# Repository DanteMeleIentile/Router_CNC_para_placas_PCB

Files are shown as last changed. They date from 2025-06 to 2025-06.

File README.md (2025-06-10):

# Router CNC para placas PCBs
Proyecto desarrollado por el Grupo 1 en la materia **Prácticas Profesionalizantes** del **Instituto Industrial Luis A. Huergo**.

**Año:** 2020

[Acceder a la carpeta del proyecto en Google Drive](https://drive.google.com/drive/folders/1eBrdESxct46WMWiOsJgtsmofHZRLYTOU?usp=sharing)

## Docentes
- Osvaldo Ivani
- Sebastían Amago Prato
- Martín A. Ricciardelli
- Juan Martín Hermida

## Estudiantes (Grupo 1)
- Dante G. Mele Ientile (Project Manager)
- León A. Martin
- Hernán A. Silva
- Nicolás L. Fertonani
- Laureano M. Rivera Pascua

---
> _"Lo que comenzó siendo una simple idea de una “Solución Electromecánica”, se
convirtió en un ensamble 3D con más de 1000 componentes, en 100 planos tanto mecánicos
como eléctricos y electrónicos, en más de 60 diagramas de operaciones, en 4 circuitos de
control, generando más de 50 GB de datos y un sinfín de avances y resultados completamente
realizadores._
>
>  _Todo esto fue el resultado de más de **5000 horas de trabajo**, en un período de prácticamente
8 meses, preservando día a día la Constancia, la Exigencia y el Compromiso."_
---

<p align="center">
  Logo Huergo
</p>

## Licencia
Este proyecto (incluyendo código, planos, documentación técnica y modelos 3D) está disponible bajo la licencia [MIT](./LICENSE).

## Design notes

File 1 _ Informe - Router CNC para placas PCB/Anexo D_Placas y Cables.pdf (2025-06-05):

## Cables y Terminales

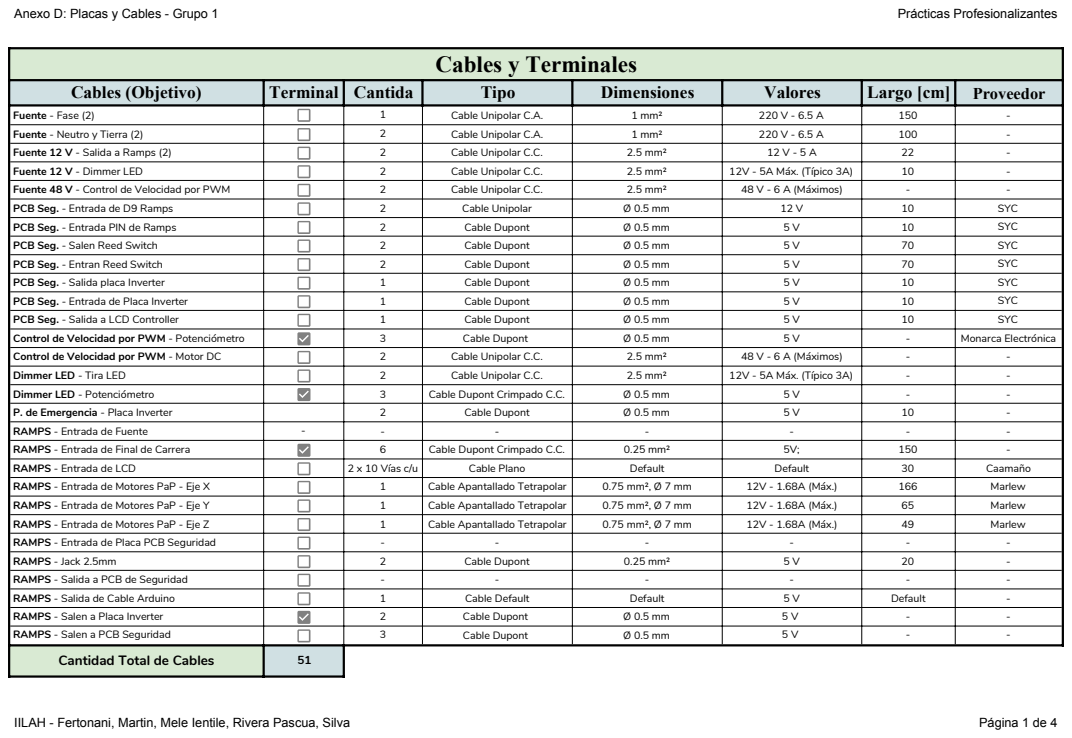
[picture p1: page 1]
Anexo D: Placas y Cables - Grupo 1; Prácticas Profesionalizantes; IILAH - Fertonani, Martin, Mele Ientile, Rivera Pascua, Silva; Página 1 de 4

Cables (Objetivo) | Terminal | Cantida | Tipo | Dimensiones | Valores | Largo [cm] | Proveedor

Fuente - Fase (2) | | 1 | Cable Unipolar C.A. | 1 mm² | 220 V - 6.5 A | 150 | -
Fuente - Neutro y Tierra (2) | | 2 | Cable Unipolar C.A. | 1 mm² | 220 V - 6.5 A | 100 | -
Fuente 12 V - Salida a Ramps (2) | | 2 | Cable Unipolar C.C. | 2.5 mm² | 12 V - 5 A | 22 | -
Fuente 12 V - Dimmer LED | | 2 | Cable Unipolar C.C. | 2.5 mm² | 12V - 5A Máx. (Típico 3A) | 10 | -
Fuente 48 V - Control de Velocidad por PWM | | 2 | Cable Unipolar C.C. | 2.5 mm² | 48 V - 6 A (Máximos) | - | -
PCB Seg. - Entrada de D9 Ramps | | 2 | Cable Unipolar | Ø 0.5 mm | 12 V | 10 | SYC
PCB Seg. - Entrada PIN de Ramps | | 2 | Cable Dupont | Ø 0.5 mm | 5 V | 10 | SYC
PCB Seg. - Salen Reed Switch | | 2 | Cable Dupont | Ø 0.5 mm | 5 V | 70 | SYC
PCB Seg. - Entran Reed Switch | | 2 | Cable Dupont | Ø 0.5 mm | 5 V | 70 | SYC
PCB Seg. - Salida placa Inverter | | 1 | Cable Dupont | Ø 0.5 mm | 5 V | 10 | SYC
PCB Seg. - Entrada de Placa Inverter | | 1 | Cable Dupont | Ø 0.5 mm | 5 V | 10 | SYC
PCB Seg. - Salida a LCD Controller | | 1 | Cable Dupont | Ø 0.5 mm | 5 V | 10 | SYC
Control de Velocidad por PWM - Potenciómetro | | 3 | Cable Dupont | Ø 0.5 mm | 5 V | - | Monarca Electrónica
Control de Velocidad por PWM - Motor DC | | 2 | Cable Unipolar C.C. | 2.5 mm² | 48 V - 6 A (Máximos) | - | -
Dimmer LED - Tira LED | | 2 | Cable Unipolar C.C. | 2.5 mm² | 12V - 5A Máx. (Típico 3A) | - | -
Dimmer LED - Potenciómetro | | 3 | Cable Dupont Crimpado C.C. | Ø 0.5 mm | 5 V | - | -
P. de Emergencia - Placa Inverter | | 2 | Cable Dupont | Ø 0.5 mm | 5 V | 10 | -
RAMPS - Entrada de Fuente | - | - | - | - | - | - | -
RAMPS - Entrada de Final de Carrera | | 6 | Cable Dupont Crimpado C.C. | 0.25 mm² | 5V; | 150 | -
RAMPS - Entrada de LCD | | 2 x 10 Vías c/u | Cable Plano | Default | Default | 30 | Caamaño
RAMPS - Entrada de Motores PaP - Eje X | | 1 | Cable Apantallado Tetrapolar | 0.75 mm², Ø 7 mm | 12V - 1.68A (Máx.) | 166 | Marlew
RAMPS - Entrada de Motores PaP - Eje Y | | 1 | Cable Apantallado Tetrapolar | 0.75 mm², Ø 7 mm | 12V - 1.68A (Máx.) | 65 | Marlew
RAMPS - Entrada de Motores PaP - Eje Z | | 1 | Cable Apantallado Tetrapolar | 0.75 mm², Ø 7 mm | 12V - 1.68A (Máx.) | 49 | Marlew
RAMPS - Entrada de Placa PCB Seguridad | | - | - | - | - | - | -
RAMPS - Jack 2.5mm | | 2 | Cable Dupont | 0.25 mm² | 5 V | 20 | -
RAMPS - Salida a PCB de Seguridad | | - | - | - | - | - | -
RAMPS - Salida de Cable Arduino | | 1 | Cable Default | Default | 5 V | Default | -
RAMPS - Salen a Placa Inverter | | 2 | Cable Dupont | Ø 0.5 mm | 5 V | - | -
RAMPS - Salen a PCB Seguridad | | 3 | Cable Dupont | Ø 0.5 mm | 5 V | - | -
Cantidad Total de Cables | 51

IILAH - Fertonani, Martin, Mele Ientile, Rivera Pascua, Silva | Página 2 de 4

## Componentes Placa Dimmer para Tira LED

Componente | Cant. | Caracteristicas | Ø broca | Código SYC | Link Datasheet
Resistencia | 1 | 1 kΩ, 1/4W | 1 | CR25S-1K | http://www.sycelectronica.com.ar/pasivos/CR25S-XX.pdf
Resistencia Gate MosFET | 1 | 56 Ω, 1/4 W | 1 | CR25S-56 | http://www.sycelectronica.com.ar/pasivos/CR25S-XX.pdf
Capacitor | 2 | 10 nF, 50V, disco cerámico | 1 | CD103-50
Capacitor | 1 | 1 µF, Radial, electrolítico aluminio | 1 | R1M50 | http://www.sycelectronica.com.ar/pasivos/RXXXMXX.pdf
Diodo rápido | 2 | 1N4148, de señal, Vr = 100 V | 1 | 1N4148 | http://www.sycelectronica.com.ar/semiconductores/1N4148.pdf
Potenciómetro Lineal | 1 | 1 MΩ | 1 | POTE-105-LIN | N.e.
LM555 | 1 | Ver datasheet | 1 | EK500A-2P | http://www.sycelectronica.com.ar/semiconductores/LM555.pdf
MOSFET | 1 | IRFZ48N, Rdson = 14 mΩ, Vds = 55 V | 1,5 | IRFZ48N | http://www.sycelectronica.com.ar/semiconductores/IRFZ48N.pdf
Bornera | 2 | 2 polos, paso = 5 mm | 1 | EK500A-2P | http://www.sycelectronica.com.ar/borneras/EK500A-XXP.pdf
Conector para Potenciómetro | 1 | Macho, 3 vías | 2 | 2317SJ-03 | http://www.sycelectronica.com.ar/conectores/PWXX.pdf
Conector para Potenciómetro | 1 | Hembra, 3 vías | 1 | PHUXX | http://www.sycelectronica.com.ar/conectores/PHUXX.pdf
Disipador | 1 | 15 x 15 x 15 | - | D-9075D | http://www.sycelectronica.com.ar/accesorios/DISIPADORES.pdf
Terminal | 3 | En rollo | - | PHUT | http://www.sycelectronica.com.ar/conectores/PHUT.pdf
Agujeros de Sujección | 4 | - | 3,5 | - | -

IILAH - Fertonani, Martin, Mele Ientile, Rivera Pascua, Silva | Página 3 de 4

## Componentes Placa Seguridad

Componente | Cant. | Caracteristicas | Ø broca | Código - SYC | Link Datasheet
Compuerta NAND | 1 | Quad NAND | 1 | 74LS00 | http://www.sycelectronica.com.ar/semiconductores/74LS00.pdf
Compuerta AND | 1 | Quad AND | 1 | 74LS08 | http://www.sycelectronica.com.ar/semiconductores/74LS08.pdf
Capacitor | 1 | 47 µF, 5x11, 16V, Electrolítico de aluminio | 1 | R47M16 | http://www.sycelectronica.com.ar/pasivos/RXXXMXX.pdf
Diodo Zener | 1 | 1N4733 | 1 | ZEN-1W-5V1 | http://www.sycelectronica.com.ar/semiconductores/ZEN-1W-XXV.pdf
Jumper con Extractor | 1 | Con extrractor | 1 | MJ02-L | http://www.sycelectronica.com.ar/conectores/MJ02-X.pdf
Pin Header | 1 | Tira de 16 | 1 | SCP16-SF | http://www.sycelectronica.com.ar/conectores/SCP16-SF.pdf
Diodo LED | 1 | Rojo, 5 mm | 1 | LED-010-15010 | http://www.sycelectronica.com.ar/optoelectronica/LED-010-15010.pdf
Resistencia Pull Down | 6 | 1 KΩ | 1 | CR25S-5K6 | http://www.sycelectronica.com.ar/pasivos/CR25S-XX.pdf
Resistencia Capacitor | 1 | 270 Ω | 1 | CR25S-270 | http://www.sycelectronica.com.ar/pasivos/CR25S-XX.pdf
Resistencia LED | 1 | 220 Ω | 1 | CR25S-220 | http://www.sycelectronica.com.ar/pasivos/CR25S-XX.pdf
Resistencia Zener | 1 | 1 KΩ | 1 | CR25S-1K | http://www.sycelectronica.com.ar/pasivos/CR25S-XX.pdf
Bornera para Cables Motor DC | 1 | 2 polos, paso = 5 mm | 2 | EK500A-2P | http://www.sycelectronica.com.ar/borneras/EK500A-XXP.pdf
Diodo Schottky | 1 | If: 1A, Vr: 30V | 1 | 1N5817 | http://www.sycelectronica.com.ar/semiconductores/1N5817-9.pdf
Relay | 1 | 12 V, 10 A | 1,5 | NT73-12 | http://www.sycelectronica.com.ar/electromecanicos/NT73-XX.pdf
Agujeros de Sujección | 4 | - | 3,5 | - | -

IILAH - Fertonani, Martin, Mele Ientile, Rivera Pascua, Silva | Página 4 de 4

## Componentes Placa Inverter

Componente | Cant. | Caracteristicas | Ø broca | Código - SYC | Link Datasheet
Compuerta NOT | 1 | Quad NAND | 1 | 74LS04 | http://www.sycelectronica.com.ar/semiconductores/74LS00.pdf
Resistencia Pull Down | 6 | 1 KΩ | 1 | CR25S-5K6 | http://www.sycelectronica.com.ar/pasivos/CR25S-XX.pdf
Pin Header | 1 | Tira de 16 | 2 | SCP16-SF | http://www.sycelectronica.com.ar/conectores/SCP16-SF.pdf
Agujeros de Fijación | 4 | Tira de 16 | 3,5 | SCP16-SF | http://www.sycelectronica.com.ar/conectores/SCP16-SF.pdf

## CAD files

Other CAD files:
8 _ Diseño 3D - Grupo 1 (Inventor)/Acolpe L para Soporte LED.ipt
8 _ Diseño 3D - Grupo 1 (Inventor)/Acople de Motor PAP.ipt
8 _ Diseño 3D - Grupo 1 (Inventor)/Acople de soporte de motor.ipt
8 _ Diseño 3D - Grupo 1 (Inventor)/Ala 1 Bisagra tipo Libro Chica.ipt
8 _ Diseño 3D - Grupo 1 (Inventor)/Ala 1 Bisagra tipo Libro Grande.ipt
8 _ Diseño 3D - Grupo 1 (Inventor)/Ala 1 Bisagra tipo T.ipt
8 _ Diseño 3D - Grupo 1 (Inventor)/Ala 2 Bisagra tipo Libro Chica.ipt
8 _ Diseño 3D - Grupo 1 (Inventor)/Ala 2 Bisagra tipo Libro Grande.ipt
8 _ Diseño 3D - Grupo 1 (Inventor)/Ala 2 Bisagra tipo T.ipt
8 _ Diseño 3D - Grupo 1 (Inventor)/Arandela Grower M4.ipt
8 _ Diseño 3D - Grupo 1 (Inventor)/Arandela Grower M8.ipt
8 _ Diseño 3D - Grupo 1 (Inventor)/Arandela Grower m6.ipt
8 _ Diseño 3D - Grupo 1 (Inventor)/Arandela Plana Tipo A DIN 125 - M4.ipt
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

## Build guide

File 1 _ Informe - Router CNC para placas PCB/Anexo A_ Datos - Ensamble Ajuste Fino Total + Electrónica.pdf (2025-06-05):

Anexo A: Datos - Ensamble Ajuste Fino Total + Electrónica - Grupo 1 | Prácticas Profesionalizantes
IILAH - Fertonani, Martin, Mele Ientile, Rivera Pascua, Silva | Página 1 de 12

# Subconjunto Inferior - Ensamble Ajuste Fino Total + Electrónica

Nombre de la Pieza | Cant. | Medias Finales | Material | Material Inventor | Código
Acople Rigído 5x8 - Eje Y | 1 | Ver hoja "Varios" | - | Flaked Satin - Blue | -
Buje para Guía | 4 | Ver hoja "Varios" | Resina Acetal | Acetal Resin White | G1-AC-01-A
Bandeja | 1 | 2 x 408 x 454 | Chapa de Al - Espesor 2mm | Al 1100 - H14 | G1 - A - 16
Buje para Tornillo - Eje Y | 1 | Ver hoja "Varios" | Latón | Brass, Soft Yellow | G1-ABC-01-A
Chaponete | 2 | 8 x 12 x 50 | Acero SAE 1020 | Steel, High Strenght, Low Alloy | G1 - A - 13
Culata | 1 | 10 x 50 x 390 | Aluminio | Aluminio 6061 | G1 - A - 02
Esquina de Bandeja | 4 | 2 x 14 x 60 | Chapa de Al - Espesor 2mm | Al 1100 - H14 | G1 - A - 17
Frente | 1 | 10 x 50 x 390 | Aluminio | Aluminio 6061 | G1 - A - 01
Guía de Bandeja Derecha | 1 | 2 x 52,7 x 425 | Chapa de Al - Espesor 2mm | Al 1100 - H14 | G1 - A - 15
Guía de Bandeja Izquierda | 1 | 3 x 52,7 x 425 | Chapa de Al - Espesor 2mm | Al 1100 - H14 | G1 - A - 14
Guía de Mesa | 2 | Ø:12,7; L:434 | Acero SAE 1040 Cromado | Steel, High Strenght, Low Alloy | G1 - A - 06
Lateral Der. | 1 | 10 x 50 x 434 | Aluminio | Aluminio 6061 | G1 - A - 04
Lateral Izq. | 1 | 10 x 50 x 434 | Aluminio | Aluminio 6061 | G1 - A - 03
Manija para Bandeja | 1 | Ver Catálogo | - | - | -
Mesa | 1 | 10 x 200 x 200 | Acero SAE 1020 | Steel Mid | G1 - A - 12
Motor Paso a Paso - Eje Y | 1 | Ver Catálogo | - | - | -
Pared Espaciador - Sub. Inferior | 2 | 10 x 16 x 42 | Aluminio | Aluminio 6061 | G1 - A - 08
Patas Regulables | 4 | Ver Catálogo - Tornillo M6 | Ver Catálogo | - | -
Resorte para Tuerca de Mesa | 1 | Ø:20; Largo: 20; Paso: 6; ØEspira: 3 | - | - | -
Soporte de Buje para Guía | 4 | 28 x 40 x 35 | Aluminio | Aluminio 6061 | G1 - A - 10
Soporte de Patas Regulables | 4 | 10 x 35 x 42 | Aluminio | Aluminio 6061 | G1 - A - 05
Soporte de Tuerca de Mesa | 1 | 40 x 50 x 42 | Aluminio | Aluminio 6061 | G1 - A - 11
Tapa para Buje | 8 | Ver "Varios" | Acero SAE 1040 Cromado | Steel, High Strenght, Low Alloy | G1-AC-02-A
Techo Espaciador - Sub. Inferior | 1 | 10 x 42 x 62 | Aluminio | Aluminio 6061 | G1 - A - 09
Tornillo de Mesa | 1 | D:12; L:434 | Acero SAE 1040 | Steel | G1 - A - 07
Tuerca de Mesa | 1 | Ver "Varios" | Latón | Brass, Soft Yellow | G1-AC-03-A

# Sujeciones

Nombre de la pieza | Cant. | Objetivo
Arandela Grower M6 | 4 | Guía con Frente/Culata
Arandela Plana M4 | 2 | Chaponete con Tornillo para Chaponete
Arandela Plana M6 | 4 | Guía con Frente/Culata
Remache POP D4 | 8 | Esquinas de Bandeja con Bandeja
Tornillo Allen C/Botón M3 L:8 | 16 | Tapa para Buje
Tornillo Allen C/Botón M4 L:10 | 6 | Guía de Bandeja con Lateral
Tornillo Allen C/Botón M6 L:20 | 8 | Frente /Culata con Laterales
Tornillo Allen C/Botón M6 L:20 | 4 | Guia Con Frente /Culata
Tornillo Allen C/Cilindrica M4 L:16 | 4 | Techo Espaciador con Motor PaP
Tornillo Allen C/Cilindrica M4 L:16 | 4 | Sop. de Tuerca con Mesa
Tornillo Allen C/Cilindrica M4 L:20 (opcional) | 2 | Chaponete con Mesa
Tornillo Allen C/Cilindrica M4 L:35 | 16 | Sop. de Buje con Mesa
Tornillo Allen C/Cilindrica M4 L:35 | 4 | Espaciador con Culata
Tornillo Allen C/Fresada M3 L:20 | 2 | Apoyo de Chaponete
Tornillo Allen C/Fresada M4 L:16 | 8 | Sop de Pata con Lateral
Tornillo Allen Gusano M3 L:16 | 2 | Tuerca con Sop. Tuerca
Tuerca Hexagonal M4 | 1 | Manija de Bandeja con Bandeja

Anexo A Datos - Ensamble Ajuste Fino Total + Electrónica - Grupo 1 | Prácticas Profesionalizantes
IILAH - Fertonani, Martin, Mele Ientile, Rivera Pascua, Silva | Página 2 de 12

# Subconjunto Puente - Ensamble Ajuste Fino Total + Electrónica

Pieza | Cant. | Medidas Finales | Material | Material Inventor | Código
Acople Rígido 5x8 - Eje X | 1 | Ver Catálogo | - | Flaked Satin - Blue | -
Buje para Tornillo - Eje X | 1 | Ver hoja "Varios" | Latón | Brass, Soft Yellow | G1-ABC-01-B
Columna Der. | 1 | 12 x 64,5 x 259,5 | Aluminio | Aluminio 6061 | G1 - B - 02
Columna Izq. | 1 | 12 x 64,5 x 259,5 | Aluminio | Aluminio 6061 | G1 - B - 01
Final de Carrera - Eje X | 1 | Ver Catálogo | - | - | -
Guías de Vínculo Cabezal | 2 | Ø:12,7; L:434 | Acero SAE 1040 Cromado | Steel, High Strenght, Low Alloy | G1 - B - 03
Motor Paso a Paso - Eje X | 1 | Ver Catálogo | - | - | -
Soporte de Final de Carrera - Eje X | 1 | 2 x 25,5 x 15 | Chapa de Al - Espesor 2mm | Al 1100 - H14 | G1 - B - 06
Tornillo de Vínculo Cabezal | 1 | Ø:12; L:338 | Acero SAE 1040 | Steel | G1 - B - 04
Travesaño Estructural | 1 | 10 x 50 x 410 | Aluminio | Aluminio 6061 | G1 - B - 05

# Sujeciones

Nombre de la pieza | Cant. | Objetivo
Arandela Grower M6 | 4 | Guía con Columna
Arandela Grower M6 | 4 | Travesaño con Columna
Arandela Grower M6 | 8 | Columna con Laterales
Arandela Plana M6 | 4 | Guía con Columna
Tornillo Allen C/Botón M3 L:8 | 2 | Sop. de Final de Carrera con Columna
Tornillo Allen C/Botón M4 L:20 | 4 | Soporte para Culata Carcasa a Travesaño
Tornillo Allen C/Botón M4 L:20 | 4 | Columna con Motor PaP
Tornillo Allen C/Botón M6 L:20 | 4 | Travesaño con Columna
Tornillo Allen C/Botón M6 L:20 | 4 | Guías con Columna
Tornillo Allen C/Botón M6 L:20 | 8 | Columna con Laterales
Tornillo Allen C/Cilindrica M2 L:12 | 2 | Sop. de Final de Carrera con F. de Carrera
Tuerca Hexagonal M2 | 2 | Sop. de Final de Carrera con F. de Carrera

IILAH - Fertonani, Martin, Mele Ientile, Rivera Pascua, Silva | Página 3 de 12

# Subconjunto Cabezal - Ensamble Ajuste Fino Total + Electrónica

Nombre de la pieza | Cant. | Medidas Finales | Material | Material Inventor | Código
Acople de Soporte de Motor | 1 | 42 x 70 x 70 | Aluminio | Aluminio 6061 | G1 - C - 12
Acople Rígido 5x8 - Eje Z | 1 | Ver hoja "Varios" | - | Flaked Satin - Blue | -
Bloque de Vínculo Cabezal | 1 | 25 x 70 x 150 | Aluminio | Aluminio 6061 | G1 - C - 1
Broca Punta de Lanza (opcional) | 1 | Ver Catálogo | - | - | -
Buje de Soporte de Motor | 4 | Ø:25; L:14 | Resina Acetal | Acetal Resin White | G1 - C - 13
Buje para Guía | 4 | Ver hoja "Varios" | Resina Acetal | Aluminium Polished | G1-AC-01-C
Buje para Tornillo - Eje Z | 1 | Ver hoja "Varios" | Latón | Brass, Soft Yellow | G1-ABC-01-C
Final de Carrera - Eje Z | 1 | Ver Catálogo | Chapa Al. - Esp.: 2mm | - | -
Guía de Soporte de Motor | 2 | Ø:12,7; L: 150 | Acero SAE 1040 Cromado | Steel, High Strenght, Low Alloy | G1 - C - 05
Motor Paso a Paso - Eje Z | 1 | Ver Catálogo | - | - | -
Pared Espacidor Izq. - Sub. Cabezal | 1 | 10 x 28 x 42 | Aluminio | Aluminio 6061 | G1 - C - 08
Pared Espacidor Der. - Sub. Cabezal | 1 | 10 x 28 x 42 | Aluminio | Aluminio 6061 | G1 - C - 09
Piso de Vínculo Cabezal | 1 | 10 x 70 x 55 | Aluminio | Aluminio 6061 | G1 - C - 04
Resorte para Tuerca de Vínculo Cabezal | 1 | Ø:20; Largo: 20; Paso: 6; ØEspira: 3 | - | - | -
Separador de Bujes | 2 | Ø:18,5; L:14 | Acero SAE 1040 Cromado | Steel, High Strenght, Low Alloy | G1 - C - 02
Motor DC | 1 | Ver Catálogo | - | Al. 6061 / Chrome Polished | -
Soporte de Motor | 1 | Ver Catálogo | - | Aluminio 6061 | -
Tapa para Buje | 4 | Ver hoja "Varios" | Acero SAE 1040 Cromado | Steel, High Strenght, Low Alloy | G1-AC-02-C
Techo de Vínculo Cabezal | 1 | 10 x 70 x 55 | Aluminio | Aluminio 6061 | G1 - C - 07
Techo Espaciador - Sub. Cabezal | 1 | 10 x 50 x 60 | Aluminio | Aluminio 6061 | G1 - C -10
Tornillo de Soporte de Motor | 1 | MF12x1,5; L:164 | Acero SAE 1040 | Steel | G1 - C - 06
Tuerca de Vínculo Cabezal | 1 | Ø:34; L:15 | Latón | Brass, Soft Yellow | G1-AC-03-C
Guía para Cable de Motor | 1 | 2 x 30 x 30 | Chapa Al. - Esp.: 2mm | Aluminio 1100 H14 | G1 - C - 11
Vertical de Vínculo Cabezal | 1 | 12 x 136 x 70 | Aluminio | Aluminio 6061 | G1 - C - 03

# Sujeciones

Nombre de la pieza | Cant. | Objetivo
Arandela Grower M6 | 4 | Guía con Techo y Piso de Vínculo Cabezal
Arandela Grower M8 | 4 | Acople de Soporte de Motor con Sop. de Motor
Arandela Plana M6 | 4 | Guía con Techo y Piso de Vínculo Cabezal
Tornillo Allen C/Botón M3 L:8 | 4 | Buje de Sop. de M. con Acople de Motor Dc
Tornillo Allen C/Botón M3 L:8 | 8 | Tapa de Buje con Bloque de Vínculo
Tornillo Allen C/Botón M3 L:8 | 2 | Guía para Cable de Motor con Pared Espacidor
Tornillo Allen C/Botón M6 L:16 | 8 | Vertical con Techo y Piso de Vínculo Cabezal
Tornillo Allen C/Botón M6 L:20 | 4 | Guía con Techo y Piso de Vínculo Cabezal
Tornillo Allen C/Botón M6 L:20 | 8 | Vertical con Bloque de Vínculo Cabezal
Tornillo Allen C/Botón M8 L:20 | 4 | Acople de Soporte de Motor con Sop. de Motor
Tornillo Allen C/Cilindrica M2 L:12 | 2 | Techo de Vínculo Cabezal con Final de Carrera
Tornillo Allen C/Cilíndrica M4 L:20 | 4 | Motor PaP con Techo de Espaciador
Tornillo Allen C/Cilindrica M4 L:45 | 4 | Paredes de Espaciador con Techo de Vínculo
Tornillo Allen Gusano M3 L:16 | 2 | Tuerca con Sop. Tuerca
Tornillo Allen Gusano M6 L:8 | 1 | Motor DC con Soporte de Motor

# Subconjunto Carcasa - Ensamble Ajuste Fino Total + Electrónica

Nombre de la pieza | Cant. | Medidas Finales | Material | Material Inventor | Código

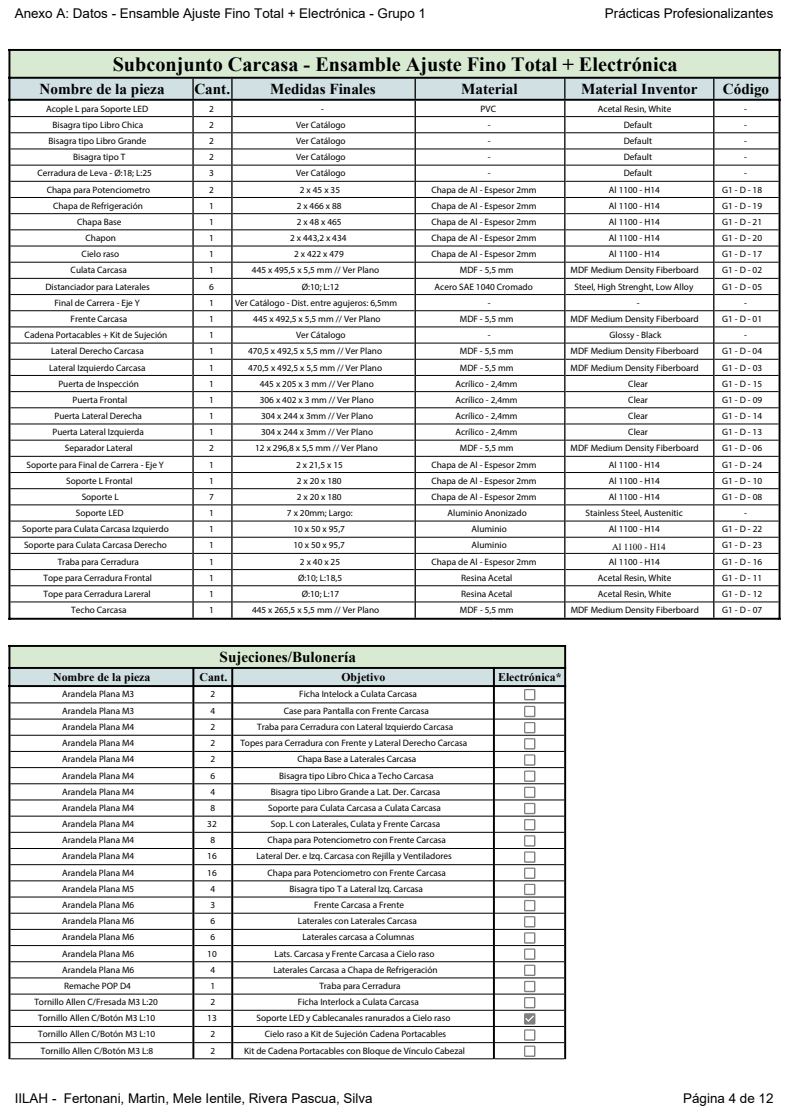
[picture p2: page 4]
IILAH - Fertonani, Martin, Mele Ientile, Rivera Pascua, Silva; Página 4 de 12

Acople L para Soporte LED | 2 | - | PVC | Acetal Resin, White | -
Bisagra tipo Libro Chica | 2 | Ver Catálogo | - | Default | -
Bisagra tipo Libro Grande | 2 | Ver Catálogo | - | Default | -
Bisagra tipo T | 2 | Ver Catálogo | - | Default | -

Cerradura de Leva - Ø:18; L:25 | 3 | Ver Catálogo | - | Default | -
Chapa para Potenciometro | 2 | 2 x 45 x 35 | Chapa de Al - Espesor 2mm | Al 1100 - H14 | G1 - D - 18
Chapa de Refrigeración | 1 | 2 x 466 x 88 | Chapa de Al - Espesor 2mm | Al 1100 - H14 | G1 - D - 19
Chapa Base | 1 | 2 x 48 x 465 | Chapa de Al - Espesor 2mm | Al 1100 - H14 | G1 - D - 21
Chapon | 1 | 2 x 443,2 x 434 | Chapa de Al - Espesor 2mm | Al 1100 - H14 | G1 - D - 20
Cielo raso | 1 | 2 x 422 x 479 | Chapa de Al - Espesor 2mm | Al 1100 - H14 | G1 - D - 17
Culata Carcasa | 1 | 445 x 495,5 x 5,5 mm // Ver Plano | MDF - 5,5 mm | MDF Medium Density Fiberboard | G1 - D - 02
Distanciador para Laterales | 6 | Ø:10; L:12 | Acero SAE 1040 Cromado | Steel, High Strenght, Low Alloy | G1 - D - 05
Final de Carrera - Eje Y | 1 | Ver Catálogo - Dist. entre agujeros: 6,5mm | - | - | -
Frente Carcasa | 1 | 445 x 492,5 x 5,5 mm // Ver Plano | MDF - 5,5 mm | MDF Medium Density Fiberboard | G1 - D - 01

Cadena Portacables + Kit de Sujeción | 1 | Ver Cátalogo | - | Glossy - Black | -
Lateral Derecho Carcasa | 1 | 470,5 x 492,5 x 5,5 mm // Ver Plano | MDF - 5,5 mm | MDF Medium Density Fiberboard | G1 - D - 04
Lateral Izquierdo Carcasa | 1 | 470,5 x 492,5 x 5,5 mm // Ver Plano | MDF - 5,5 mm | MDF Medium Density Fiberboard | G1 - D - 03
Puerta de Inspección | 1 | 445 x 205 x 3 mm // Ver Plano | Acrílico - 2,4mm | Clear | G1 - D - 15
Puerta Frontal | 1 | 306 x 402 x 3 mm // Ver Plano | Acrílico - 2,4mm | Clear | G1 - D - 09
Puerta Lateral Derecha | 1 | 304 x 244 x 3mm // Ver Plano | Acrílico - 2,4mm | Clear | G1 - D - 14
Puerta Lateral Izquierda | 1 | 304 x 244 x 3mm // Ver Plano | Acrílico - 2,4mm | Clear | G1 - D - 13
Separador Lateral | 2 | 12 x 296,8 x 5,5 mm // Ver Plano | MDF - 5,5 mm | MDF Medium Density Fiberboard | G1 - D - 06

Soporte para Final de Carrera - Eje Y | 1 | 2 x 21,5 x 15 | Chapa de Al - Espesor 2mm | Al 1100 - H14 | G1 - D - 24

Soporte L Frontal | 1 | 2 x 20 x 180 | Chapa de Al - Espesor 2mm | Al 1100 - H14 | G1 - D - 10
Soporte L | 7 | 2 x 20 x 180 | Chapa de Al - Espesor 2mm | Al 1100 - H14 | G1 - D - 08
Soporte LED | 1 | 7 x 20mm; Largo: | Aluminio Anonizado | Stainless Steel, Austenitic | -

Soporte para Culata Carcasa Izquierdo | 1 | 10 x 50 x 95,7 | Aluminio | Al 1100 - H14 | G1 - D - 22
Soporte para Culata Carcasa Derecho | 1 | 10 x 50 x 95,7 | Aluminio | Al 1100 - H14 | G1 - D - 23

Traba para Cerradura | 1 | 2 x 40 x 25 | Chapa de Al - Espesor 2mm | Al 1100 - H14 | G1 - D - 16
Tope para Cerradura Frontal | 1 | Ø:10; L:18,5 | Resina Acetal | Acetal Resin, White | G1 - D - 11
Tope para Cerradura Lareral | 1 | Ø:10; L:17 | Resina Acetal | Acetal Resin, White | G1 - D - 12
Techo Carcasa | 1 | 445 x 265,5 x 5,5 mm // Ver Plano | MDF - 5,5 mm | MDF Medium Density Fiberboard | G1 - D - 07

Sujeciones/Bulonería

Nombre de la pieza | Cant. | Objetivo | Electrónica*
Arandela Plana M3 | 2 | Ficha Intelock a Culata Carcasa
Arandela Plana M3 | 4 | Case para Pantalla con Frente Carcasa
Arandela Plana M4 | 2 | Traba para Cerradura con Lateral Izquierdo Carcasa
Arandela Plana M4 | 2 | Topes para Cerradura con Frente y Lateral Derecho Carcasa
Arandela Plana M4 | 2 | Chapa Base a Laterales Carcasa
Arandela Plana M4 | 6 | Bisagra tipo Libro Chica a Techo Carcasa
Arandela Plana M4 | 4 | Bisagra tipo Libro Grande a Lat. Der. Carcasa
Arandela Plana M4 | 8 | Soporte para Culata Carcasa a Culata Carcasa
Arandela Plana M4 | 32 | Sop. L con Laterales, Culata y Frente Carcasa
Arandela Plana M4 | 8 | Chapa para Potenciometro con Frente Carcasa
Arandela Plana M4 | 16 | Lateral Der. e Izq. Carcasa con Rejilla y Ventiladores
Arandela Plana M4 | 16 | Chapa para Potenciometro con Frente Carcasa
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

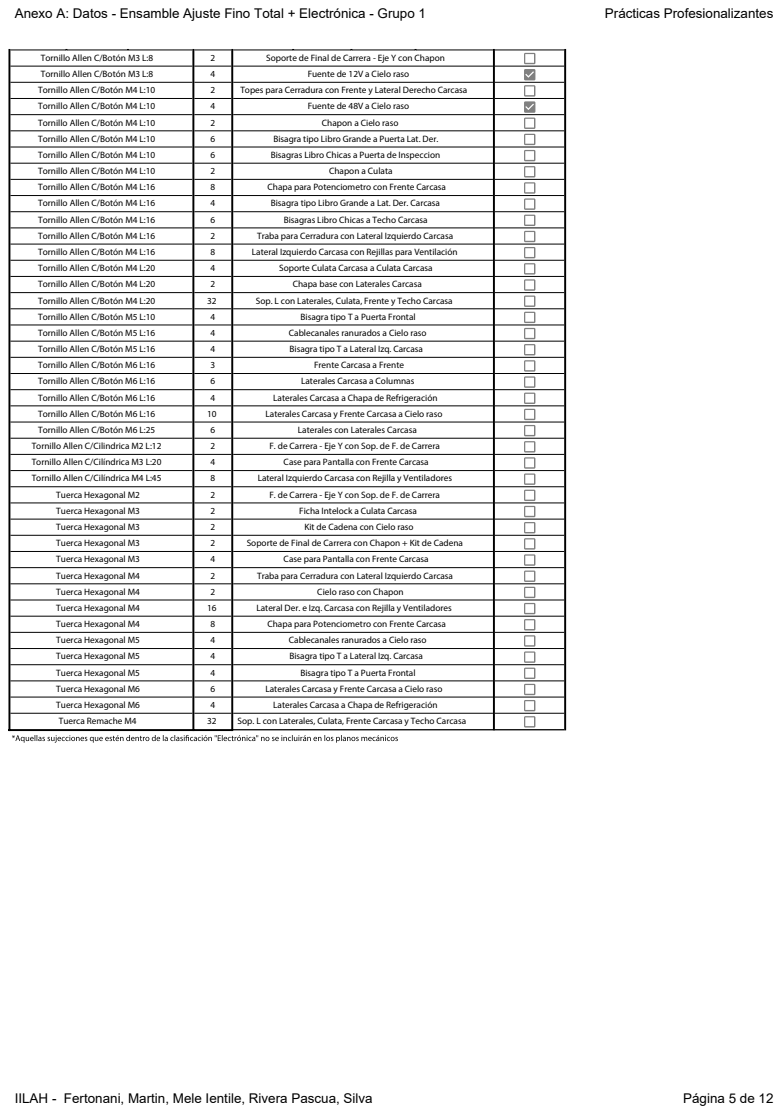
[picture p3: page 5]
IILAH - Fertonani, Martin, Mele Ientile, Rivera Pascua, Silva; Página 5 de 12

Tornillo Allen C/Botón M3 L:8 | 2 | Soporte de Final de Carrera - Eje Y con Chapon
Tornillo Allen C/Botón M3 L:8 | 4 | Fuente de 12V a Cielo raso
Tornillo Allen C/Botón M4 L:10 | 2 | Topes para Cerradura con Frente y Lateral Derecho Carcasa
Tornillo Allen C/Botón M4 L:10 | 4 | Fuente de 48V a Cielo raso
Tornillo Allen C/Botón M4 L:10 | 2 | Chapon a Cielo raso
Tornillo Allen C/Botón M4 L:10 | 6 | Bisagra tipo Libro Grande a Puerta Lat. Der.
Tornillo Allen C/Botón M4 L:10 | 6 | Bisagras Libro Chicas a Puerta de Inspeccion
Tornillo Allen C/Botón M4 L:10 | 2 | Chapon a Culata
Tornillo Allen C/Botón M4 L:16 | 8 | Chapa para Potenciometro con Frente Carcasa
Tornillo Allen C/Botón M4 L:16 | 4 | Bisagra tipo Libro Grande a Lat. Der. Carcasa
Tornillo Allen C/Botón M4 L:16 | 6 | Bisagras Libro Chicas a Techo Carcasa
Tornillo Allen C/Botón M4 L:16 | 2 | Traba para Cerradura con Lateral Izquierdo Carcasa
Tornillo Allen C/Botón M4 L:16 | 8 | Lateral Izquierdo Carcasa con Rejillas para Ventilación
Tornillo Allen C/Botón M4 L:20 | 4 | Soporte Culata Carcasa a Culata Carcasa
Tornillo Allen C/Botón M4 L:20 | 2 | Chapa base con Laterales Carcasa
Tornillo Allen C/Botón M4 L:20 | 32 | Sop. L con Laterales, Culata, Frente y Techo Carcasa
Tornillo Allen C/Botón M5 L:10 | 4 | Bisagra tipo T a Puerta Frontal
Tornillo Allen C/Botón M5 L:16 | 4 | Cablecanales ranurados a Cielo raso
Tornillo Allen C/Botón M5 L:16 | 4 | Bisagra tipo T a Lateral Izq. Carcasa
Tornillo Allen C/Botón M6 L:16 | 3 | Frente Carcasa a Frente
Tornillo Allen C/Botón M6 L:16 | 6 | Laterales Carcasa a Columnas
Tornillo Allen C/Botón M6 L:16 | 4 | Laterales Carcasa a Chapa de Refrigeración
Tornillo Allen C/Botón M6 L:16 | 10 | Laterales Carcasa y Frente Carcasa a Cielo raso
Tornillo Allen C/Botón M6 L:25 | 6 | Laterales con Laterales Carcasa
Tornillo Allen C/Cilindrica M2 L:12 | 2 | F. de Carrera - Eje Y con Sop. de F. de Carrera
Tornillo Allen C/Cilíndrica M3 L:20 | 4 | Case para Pantalla con Frente Carcasa
Tornillo Allen C/Cilíndrica M4 L:45 | 8 | Lateral Izquierdo Carcasa con Rejilla y Ventiladores
Tuerca Hexagonal M2 | 2 | F. de Carrera - Eje Y con Sop. de F. de Carrera
Tuerca Hexagonal M3 | 2 | Ficha Intelock a Culata Carcasa
Tuerca Hexagonal M3 | 2 | Kit de Cadena con Cielo raso
Tuerca Hexagonal M3 | 2 | Soporte de Final de Carrera con Chapon + Kit de Cadena
Tuerca Hexagonal M3 | 4 | Case para Pantalla con Frente Carcasa
Tuerca Hexagonal M4 | 2 | Traba para Cerradura con Lateral Izquierdo Carcasa
Tuerca Hexagonal M4 | 2 | Cielo raso con Chapon
Tuerca Hexagonal M4 | 16 | Lateral Der. e Izq. Carcasa con Rejilla y Ventiladores
Tuerca Hexagonal M4 | 8 | Chapa para Potenciometro con Frente Carcasa
Tuerca Hexagonal M5 | 4 | Cablecanales ranurados a Cielo raso
Tuerca Hexagonal M5 | 4 | Bisagra tipo T a Lateral Izq. Carcasa
Tuerca Hexagonal M5 | 4 | Bisagra tipo T a Puerta Frontal
Tuerca Hexagonal M6 | 6 | Laterales Carcasa y Frente Carcasa a Cielo raso
Tuerca Hexagonal M6 | 4 | Laterales Carcasa a Chapa de Refrigeración
Tuerca Remache M4 | 32 | Sop. L con Laterales, Culata, Frente Carcasa y Techo Carcasa

IILAH - Fertonani, Martin, Mele Ientile, Rivera Pascua, Silva | Página 6 de 12

# Varios - Ensamble Ajuste Fino Total + Electrónica

Nombre de la pieza | Cant. | Medias Finales | Material | Material Inventor | Código
Acoples Rígidos | 3 | 5-8; Ø:=14; L=25 | Ver Catálogo | Flaked Satin - Blue | -
Buje para Guía | 8 | Ø:19; L:28 | Resina | Acetal Resin White | G1 - AC - 01 - A/C
Tapa para Buje | 12 | Ø:33; L:3 | Acero SAE 1040 Cromado | Steel, High Strenght, Low Alloy | G1 - AC - 02 - A/C
Tuerca de Mesa y de Vínculo Cabezal | 2 | Ø:34; L:15; | Latón | Aluminio 6061 | G1 - AC - 03 - A/C
Dispositivo de Mecanizado | 1 | Ø:18; L: 64 | Acero SAE 1040 Cromado | Steel, High Strenght, Low Alloy | G1 - ABC - 02
Bujes para Tornillos | 3 | Ø:24; L:12 | Latón | Brass, Soft Yellow | G1 - ABC - 01 - A/B/C

IILAH - Fertonani, Martin, Mele Ientile, Rivera Pascua, Silva | Página 7 de 12

# Bulonería - Ensamble Ajuste Fino Total + Electrónica

Elemento | Tipo | Largo Cantidad Subconjunto | | | Material Inventor
Arandela M3 | Plana | - | 6 | D | Default
Arandela M4 | Plana | - | 94 | A, D | Default
Arandela M5 | Plana | - | 4 | D | Default
Arandela M6 | Grower | - | 24 | A, B, C | Rubber Blue
Arandela M6 | Plana | - | 41 | A, B, C , D | Default
Arandela M8 | Grower | - | 4 | C | Rubber Blue
M2 | C. Cilíndrica | 12 | 6 | B, C, D | Rubber Black
M3 | Gusano | 16 | 4 | A, C | Rubber Black
M3 | C. Botón | 8 | 40 | A, B, C , D | Rubber Black
M3 | C. Botón | 10 | 15 | D | Rubber Black
M3 | C. Fresada | 20 | 4 | A, D | Rubber Black
M3 | C. Cilíndrica | 20 | 4 | A | Rubber Black
M4 | C. Cilíndrica | 16 | 8 | A | Rubber Black
M4 | C. Cilíndrica | 20 | 6 | A, C | Rubber Black
M4 | C. Cilíndrica | 35 | 20 | A | Rubber Black
M4 | C. Cilíndrica | 45 | 12 | C, D | Rubber Black
M4 | C. Botón | 10 | 28 | A, D | Rubber Black
M4 | C. Botón | 16 | 28 | D | Rubber Black
M4 | C. Botón | 20 | 46 | B, D | Rubber Black
M4 | C. Fresada | 16 | 8 | A | Rubber Black
M5 | C. Botón | 10 | 4 | D | Rubber Black
M5 | C. Botón | 16 | 8 | D | Rubber Black
M6 | C. Botón | 16 | 31 | C, D | Rubber Black
M6 | C. Botón | 20 | 44 | A, B, C | Rubber Black
M6 | C. Botón | 25 | 6 | D | Rubber Black
M8 | C. Botón | 20 | 4 | C | Rubber Black
Remache pop D4 | Abierto con rotura de bástago | IILAH | 9 | A | Aluminio 7175 T73 0 Hot Formed
Tuerca Remache POP M4 | Tuerca Remache M4 | 11,6 | 32 | D | Satin - Lemon Chion
Tuerca Hexagonal M2 | Hexagonal | - | 4 | B, D | ISO 4032
Tuerca Hexagonal M3 | Hexagonal | - | 10 | D | ISO 4032
Tuerca Hexagonal M4 | Hexagonal | - | 29 | A, D | ISO 4032
Tuerca Hexagonal M5 | Hexagonal | - | 12 | D | ISO 4032
Tuerca Hexagonal M6 | Hexagonal | - | 10 | D | ISO 4032
Cant. Total de Tornillos | 326 | Cant. Total de Arandelas | 173 | Cant. Total de Tuercas | 65

IILAH -Fertonani, Martin, Mele Ientile, Rivera Pascua, Silva | Página 8 de 12

# Componentes Electrónicos - Ensamble Ajuste Fino Total + Electrónica

Componentes/Elemento | Cant. | Med. Finales | Objetivo | Material Inventor | Sujección/Bulonería Utilizada
Tecla On/O Roja | 1 | Ver Catálogo | Encender Tira LED | - | -
Tecla On/O Negra | 1 | Ver Catálogo | Encender Máquina | - | -
Parada de Emergencia | 1 | Ver Catálogo | Parada de Emergencia | - | -
LCD Controller | 1 | Ver Catálogo | Controlador | - | -
Potenciometro para Dimmer Tira LED | 1 | - | Variar Intesidad de la Tira LED | - | -
Potenciometro para Dimmer Motor DC | 1 | - | Variar Velocidad de Husillo | - | -
Jack 2,5mm | 1 | Ver Catálogo | Conexón para Auto-nivelación | - | -
PortaLED | 1 | Ver Catálogo | PortaLED indicador Auto-nivelación | - | -
Ventilador + Rejillas | 2 | Ver Catálogo | Extracción de Aire - Sección Electrónica | - | 4 Allen C/Cilíndrica M4; L:45 - Arandelas M4 y Tuercas M4
Rejilla para Ventilador | 2 | Ver Catálogo | Extracción de Aire - Sección Electrónica | - | 4 Allen C/Botón M4; L:16 - Arandelas M4 y Tuercas M4
Case para LCD Controller | 1 | Ver Catálogo | Contener LCD Controller | - | 4 Allen C/Cilíndrica M3; L: 20 - Arandelas M3 y Tuercas
Cablecanal Ranurado Vertical L:130 | 1 | L: 130mm; 30x30 | Ocultar cables | Acetal Resin White | 2 Allen C/Botón M5; L:16 - Tuerca M5
Cablecanal Ranurado Vertical L:150 | 1 | L: 148mm; 30x31 | Ocultar cables | Acetal Resin White | 2 Allen C/Botón M5; L:16 - Tuerca M5
Cablecanal Ranurado Horizontal L:340 | 1 | L: 340mm; 30x32 | Ocultar cables | Acetal Resin White | 2 Allen C/Botón M3; L:10 - Tuerca M3
Cablecanal Ranurado Horizontal L:300 | 1 | L: 300mm; 30x33 | Ocultar cables | Acetal Resin White | 2 Allen C/Botón M3; L:10 - Tuerca M3
Sop. LED L:354 (Horizontal) | 3 | L: 324mm; 20x7 | Contener la Tira LED - Horizotal | Stainless Steel Austenitic | 7 Allen C/Botón M3; L:10 - Tuerca M3
Sop. LED L:320 (Vertical) | 2 | L: 320mm; 20x7 | Contener la Tira LED - Vertical | Stainless Steel Austenitic | 6 Allen C/Botón M3; L:10 - Tuerca M3
Acople L para Sop. LED | 2 | - | Vista a los cortes de Sop. LED | Acetal Resin White | -
Imán de Neodimio | 2 | 3x8 | Accionar Reed Switch | Aluminium 6061 - AHC | Clavado con pegamento
Placa Reed Switch 30x25 + Carcasa | 1 | 30 x 25 x 2 | Sostener Reed Swich | - | 2 Tornillos M3 L:8 // 2 Tornillos M3 L:6
Carcasa para Placa Reed Switch 30x25 | 1 | - | Proteger Placa para Reed Switch | - | Idem
Placa Reed Switch 40x20 | 1 | 40 x 20 x 2 | Sostener Reed Swich | - | 2 Tornillos M3 L:8 // 2 Tornillos M3 L:4 o L:5
Carcasa para Placa Reed Switch 40x20 | 1 | - | Proteger Placa para Reed Switch | - | 2 Tornillos Allen C/Botón M4 L:16 con Arandelas y Tuercas
Espaciadores para Electrónica 5mm | 4 | 5mm - Métrica 3 | Espaciadores para Placa Reed Switch | Acetal Resin White | -
Espaciadores para Electrónica 10mm | 18 | 10mm - Métrica 3 | Espaciadores para Placas | Acetal Resin White | -
Placa Dimmer para Motor DC | 1 | 60 x 65 | Dimmer para Motor DC | - | 4 Tornillos M3 L:6
Placa Dimmer para LED | 1 | 50 x 50 | Dimer para Tira LED | - | 4 Tornillos M3 L:6
Placa Circuito de Seguridad | 1 | 50 x 50 | Seguridad de la Máquina | - | 4 Tornillos M3 L:6
Ramps 1.4 + Arduino Mega | 1 | Ver Catálogo | Controlar Máquina | - | 4 Tornillos M3 L:6
Placa Inverter | 1 | 30 x 30 | Inversión Lógica para P. de Emergencia | - | 2 Tornillos M3 L:6
Fuente 48V; 10A | 1 | Ver Catálogo | Alimentación Electrónica | - | Tornillo Allen C/Botón M4 L:10
Fuente 12V; 12,5A | 1 | Ver Catálogo | Alimentación Electrónica | - | Tornillo Allen C/Botón M3 L:8
Ficha Interlock | 1 | Ver Catálogo | Alimentación Máquina | - | 2 Tornillos Allen C/Fresada M3 L:20 - Arandelas y Tuercas
Placa USB-B | 1 | Ver Catálogo | Conexón Serie | - | 2 Tornillos M3 L:8
Espaciador Roscado | 2 | Ver Catálogo | Sujección Placa USB-B | Acetal Resin White | -

# Agrupación de Materiales Mecánicos - Ajuste Fino Total + Electrónica

Nombre de la Pieza | Sub. | Cant. | Medidas Finales | Material | Cotizado | Agrupación | Observaciones

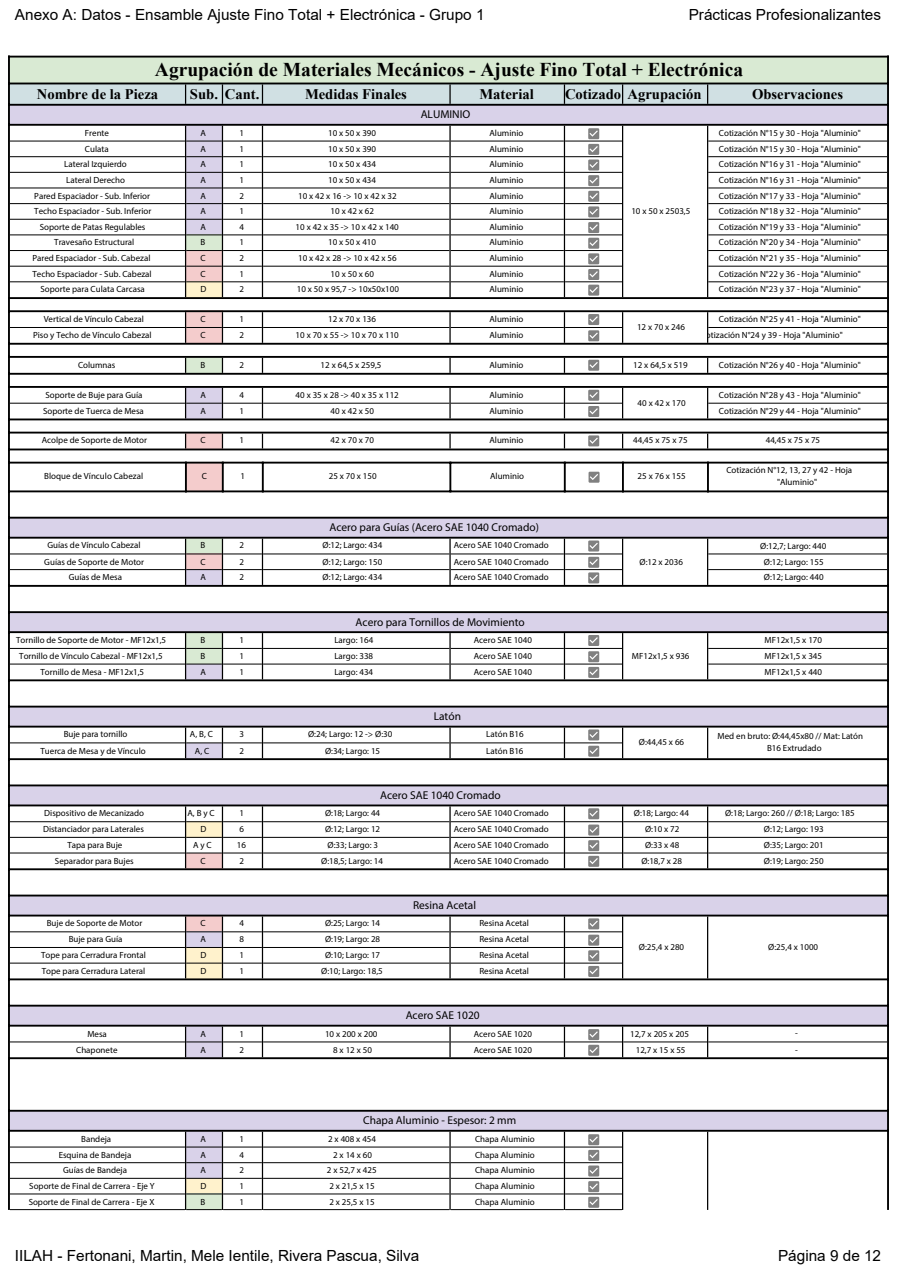
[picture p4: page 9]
IILAH - Fertonani, Martin, Mele Ientile, Rivera Pascua, Silva; Página 9 de 12; ALUMINIO; Columnas; Aluminio; Cotización N°26 y 40 - Hoja "Aluminio"; Acolpe de Soporte de Motor; Bloque de Vínculo Cabezal; Cotización N°12, 13, 27 y 42 - Hoja; "Aluminio"; Latón; Resina Acetal; Acero SAE 1020

Frente | A | 1 | 10 x 50 x 390 | Aluminio | 10 x 50 x 2503,5 | Cotización N°15 y 30 - Hoja "Aluminio"
Culata | A | 1 | 10 x 50 x 390 | Aluminio | | Cotización N°15 y 30 - Hoja "Aluminio"
Lateral Izquierdo | A | 1 | 10 x 50 x 434 | Aluminio | | Cotización N°16 y 31 - Hoja "Aluminio"
Lateral Derecho | A | 1 | 10 x 50 x 434 | Aluminio | | Cotización N°16 y 31 - Hoja "Aluminio"
Pared Espaciador - Sub. Inferior | A | 2 | 10 x 42 x 16 -> 10 x 42 x 32 | Aluminio | | Cotización N°17 y 33 - Hoja "Aluminio"
Techo Espaciador - Sub. Inferior | A | 1 | 10 x 42 x 62 | Aluminio | | Cotización N°18 y 32 - Hoja "Aluminio"
Soporte de Patas Regulables | A | 4 | 10 x 42 x 35 -> 10 x 42 x 140 | Aluminio | | Cotización N°19 y 33 - Hoja "Aluminio"
Travesaño Estructural | B | 1 | 10 x 50 x 410 | Aluminio | | Cotización N°20 y 34 - Hoja "Aluminio"
Pared Espaciador - Sub. Cabezal | C | 2 | 10 x 42 x 28 -> 10 x 42 x 56 | Aluminio | | Cotización N°21 y 35 - Hoja "Aluminio"
Techo Espaciador - Sub. Cabezal | C | 1 | 10 x 50 x 60 | Aluminio | | Cotización N°22 y 36 - Hoja "Aluminio"
Soporte para Culata Carcasa | D | 2 | 10 x 50 x 95,7 -> 10x50x100 | Aluminio | | Cotización N°23 y 37 - Hoja "Aluminio"

Vertical de Vínculo Cabezal | C | 1 | 12 x 70 x 136 | Aluminio | 12 x 70 x 246 | Cotización N°25 y 41 - Hoja "Aluminio"
Piso y Techo de Vínculo Cabezal | C | 2 | 10 x 70 x 55 -> 10 x 70 x 110 | Aluminio | Cotización N°24 y 39 - Hoja "Aluminio"

Soporte de Buje para Guía | A | 4 | 40 x 35 x 28 -> 40 x 35 x 112 | Aluminio | 40 x 42 x 170 | Cotización N°28 y 43 - Hoja "Aluminio"
Soporte de Tuerca de Mesa | A | 1 | 40 x 42 x 50 | Aluminio | | Cotización N°29 y 44 - Hoja "Aluminio"

Acero para Guías (Acero SAE 1040 Cromado)

Guías de Vínculo Cabezal | B | 2 | Ø:12; Largo: 434 | Acero SAE 1040 Cromado | Ø:12 x 2036 | Ø:12,7; Largo: 440
Guías de Soporte de Motor | C | 2 | Ø:12; Largo: 150 | Acero SAE 1040 Cromado | | Ø:12; Largo: 155
Guías de Mesa | A | 2 | Ø:12; Largo: 434 | Acero SAE 1040 Cromado | | Ø:12; Largo: 440

Acero para Tornillos de Movimiento

Tornillo de Soporte de Motor - MF12x1,5 | B | 1 | Largo: 164 | Acero SAE 1040 | MF12x1,5 x 936 | MF12x1,5 x 170
Tornillo de Vínculo Cabezal - MF12x1,5 | B | 1 | Largo: 338 | Acero SAE 1040 | | MF12x1,5 x 345
Tornillo de Mesa - MF12x1,5 | A | 1 | Largo: 434 | Acero SAE 1040 | | MF12x1,5 x 440

Buje para tornillo | A, B, C | 3 | Ø:24; Largo: 12 -> Ø:30 | Latón B16 | Ø:44,45 x 66 | Med en bruto: Ø:44,45x80 // Mat: Latón B16 Extrudado
Tuerca de Mesa y de Vínculo | A, C | 2 | Ø:34; Largo: 15 | Latón B16

Acero SAE 1040 Cromado

Dispositivo de Mecanizado | A, B y C | 1 | Ø:18; Largo: 44 | Acero SAE 1040 Cromado | Ø:18; Largo: 44 | Ø:18; Largo: 260 // Ø:18; Largo: 185
Distanciador para Laterales | D | 6 | Ø:12; Largo: 12 | Acero SAE 1040 Cromado | Ø:10 x 72 | Ø:12; Largo: 193
Tapa para Buje | A y C | 16 | Ø:33; Largo: 3 | Acero SAE 1040 Cromado | Ø:33 x 48 | Ø:35; Largo: 201
Separador para Bujes | C | 2 | Ø:18,5; Largo: 14 | Acero SAE 1040 Cromado | Ø:18,7 x 28 | Ø:19; Largo: 250

Buje de Soporte de Motor | C | 4 | Ø:25; Largo: 14 | Resina Acetal | Ø:25,4 x 280
A | 8 | Ø:19; Largo: 28 | Resina Acetal | Ø:25,4 x 1000 Buje para Guía
Tope para Cerradura Frontal | D | 1 | Ø:10; Largo: 17 | Resina Acetal
Tope para Cerradura Lateral | D | 1 | Ø:10; Largo: 18,5 | Resina Acetal

Mesa | A | 1 | 10 x 200 x 200 | Acero SAE 1020 | 12,7 x 205 x 205 | -
Chaponete | A | 2 | 8 x 12 x 50 | Acero SAE 1020 | 12,7 x 15 x 55 | -

Chapa Aluminio - Espesor: 2 mm

Bandeja | A | 1 | 2 x 408 x 454 | Chapa Aluminio
Esquina de Bandeja | A | 4 | 2 x 14 x 60 | Chapa Aluminio
Guías de Bandeja | A | 2 | 2 x 52,7 x 425 | Chapa Aluminio

Soporte de Final de Carrera - Eje Y | D | 1 | 2 x 21,5 x 15 | Chapa Aluminio
Soporte de Final de Carrera - Eje X | B | 1 | 2 x 25,5 x 15 | Chapa Aluminio

IILAH - Fertonani, Martin, Mele Ientile, Rivera Pascua, Silva | Página 10 de 12

# Agrupación de Materiales Mecánicos - Ajuste Fino Total + Electrónica

Nombre de la Pieza | Sub. | Cant. | Medidas Finales | Material | Cotizado | Agrupación | Observaciones
Guía para Cable de Motor | C | 1 | 2 x 30 x 30 | Chapa Aluminio | | 2 x 1000 x 1000
| D | 1 | 2 x 48 x 465 | Chapa Aluminio | | - Chapa Base
Chapon | D | 1 | 2 x 443,2 x 434 | Chapa Aluminio
Cielo Raso | D | 1 | 2 x 422 x 479 | Chapa Aluminio
Traba para Cerradura | D | 2 | 2 x 25 x 40 | Chapa Aluminio
Chapa para Potenciometro | D | 2 | 2 x 35 x 45 | Chapa Aluminio
Chapa para Refrigeración | D | 1 | 2 x 73 x 466 | Chapa Aluminio
Soporte L | D | 7 | 2 x 20 x 180 | Chapa Aluminio
Soporte L Frontal | D | 1 | 2 x 20 x 180 | Chapa Aluminio

Anexo A: Datos - Ensamble Ajuste Fino Total + Electrónica - Grupo 1 | Practicas Profesionales

# Planos y Máquinas a Utilizar - Ensamble Ajuste Fino Total + Electrónica

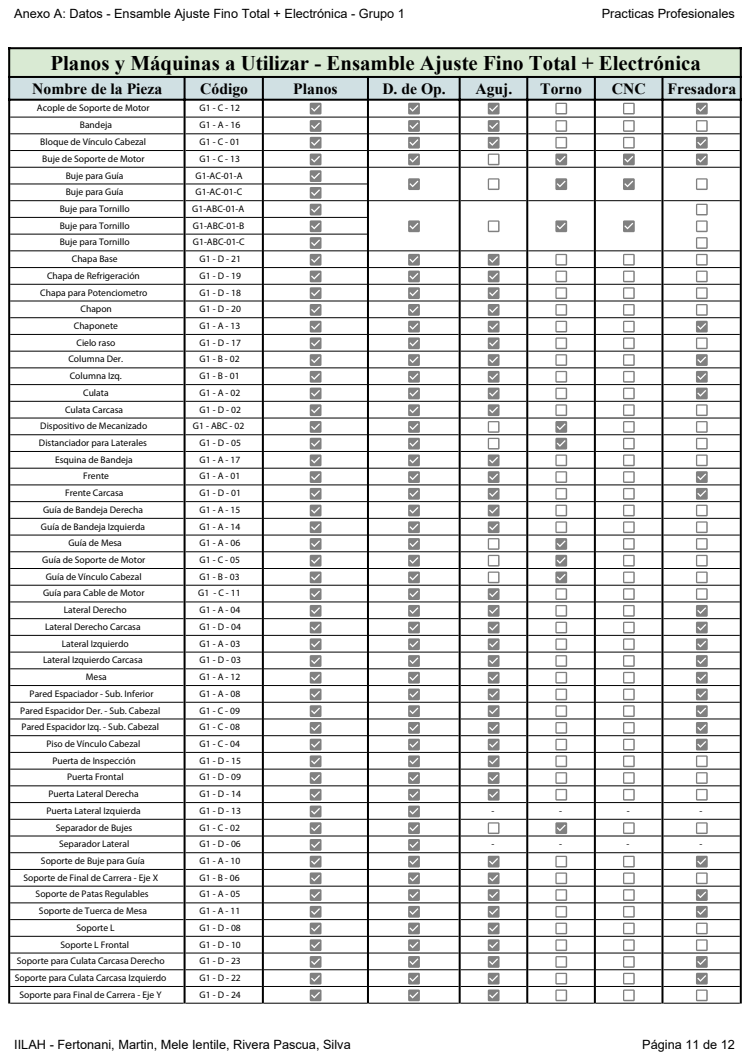
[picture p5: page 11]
IILAH - Fertonani, Martin, Mele Ientile, Rivera Pascua, Silva; Página 11 de 12; Nombre de la Pieza; Código; Planos; Aguj.; Torno; CNC; Fresadora; Acople de Soporte de Motor; Bandeja; Bloque de Vínculo Cabezal; Buje de Soporte de Motor; Buje para Guía; Buje para Tornillo; G1-ABC-01-A; G1-ABC-01-B; G1-ABC-01-C; Chapa Base; Chapa de Refrigeración; Chapa para Potenciometro; Chapon; Chaponete; Cielo raso; Columna Der.; Columna Izq.; Culata; Culata Carcasa; Dispositivo de Mecanizado; G1 - ABC - 02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

Anexo A: Datos - Ensamble Ajuste Fino Total + Electrónica - Grupo 1 | Practicas Profesionales

# Planos y Máquinas a Utilizar - Ensamble Ajuste Fino Total + Electrónica

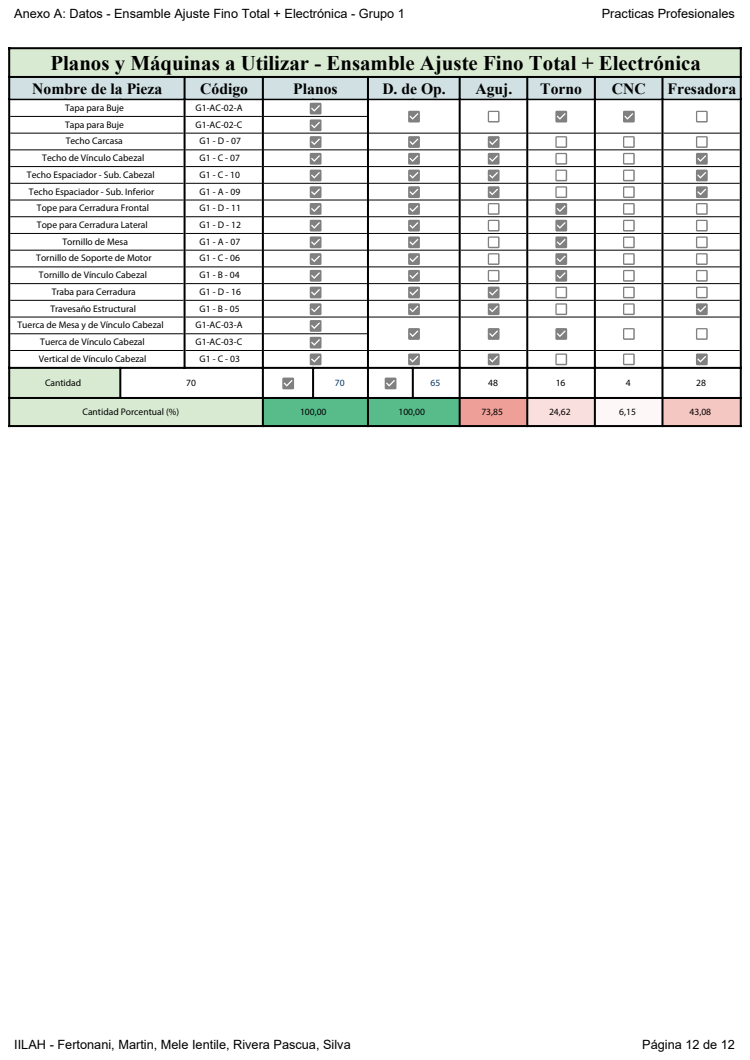
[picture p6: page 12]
IILAH - Fertonani, Martin, Mele Ientile, Rivera Pascua, Silva; Página 12 de 12

Nombre de la Pieza | Código | Planos | D. de Op. | Aguj. | Torno | CNC | Fresadora

Tapa para Buje | G1-AC-02-A
Tapa para Buje | G1-AC-02-C
Techo Carcasa | G1 - D - 07
Techo de Vínculo Cabezal | G1 - C - 07
Techo Espaciador - Sub. Cabezal | G1 - C - 10
Techo Espaciador - Sub. Inferior | G1 - A - 09
Tope para Cerradura Frontal | G1 - D - 11
Tope para Cerradura Lateral | G1 - D - 12
Tornillo de Mesa | G1 - A - 07
Tornillo de Soporte de Motor | G1 - C - 06
Tornillo de Vínculo Cabezal | G1 - B - 04
Traba para Cerradura | G1 - D - 16
Travesaño Estructural | G1 - B - 05
Tuerca de Mesa y de Vínculo Cabezal | G1-AC-03-A
Tuerca de Vínculo Cabezal | G1-AC-03-C
Vertical de Vínculo Cabezal | G1 - C - 03

Cantidad | 70 | | 70 | | 65 | 48 | 16 | 4 | 28

Cantidad Porcentual (%) | | 100,00 | | 100,00 | | 73,85 | 24,62 | 6,15 | 43,08

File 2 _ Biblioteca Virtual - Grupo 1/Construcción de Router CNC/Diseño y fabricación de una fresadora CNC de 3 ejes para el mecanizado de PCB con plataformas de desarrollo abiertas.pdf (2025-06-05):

# Diseño y fabricación de una fresadora CNC de 3 ejes para el mecanizado de PCB con plataformas de desarrollo abiertas

Titulación: | Grado en Ingeniería Electrónica
| Industrial y Automática

### Intensificación:

Alumno/a: | Miguel Riquelme García
Director/a/s: | Rosendo Zamora Pedreño

### Cartagena, 24 de Agosto de 2014

Diseño y fabricación de una fresadora CNC de 3 ejes para el mecanizado de PCB con plataformas de desarrollo abiertas Miguel Riquelme García

# ÍNDICE

### 3.5 Interfase máquina - ordenador | 60

### 3.5.1 Configuración de GRBL Controller | 64

### 4. EJEMPLO DE MECANIZADO | 65

### 5. MEMORIA ECONÓMICA | 70

### 6. CONCLUSIONES. REALIMENTACIÓN | 72

### 7. BIBLIOGRAFÍA | 74

### 7.1 Webgrafía | 74

### 7.2 Bibliografía | 74

### 7.3 Manuales | 74

TABLA DE ILUSTRACIONES | 75
ANEJO I. MOTORES PASO A PASO | 77
ANEJO II. CÓDIGO G SOPORTADO POR GRBL | 77
ANEJO III. REVISIONES DE GRBL CONTROLLER | 77
ANEJO IV. COMANDOS DE GRBL | 77
ANEJO V. PLANOS | 77

Agradecimientos:

A mi Padre.

A Antonio Ruiz Bravo.

## 1. OBJETIVOS

El presente proyecto tiene por objeto crear un dispositivo de control numérico computerizado (CNC), lo cual implica su diseño previo en 3D sobre un programa CAD, su fabricación, la implementación de la electrónica y la creación de una pieza mecanizada de ejemplo.

Para llevar a cabo esto, la ejecución de ha dividido en diferentes metas secuenciales con los siguientes condicionantes:

■ Dispositivo de bajo coste

Se trata de un compromiso entre el precio y el resultado. No tiene sentido gastar una gran cantidad de dinero en su creación ya que de este modo la solución obvia es adquirir un dispositivo desde un fabricante. No obstante, la máquina debe de tener robustez y calidad adecuada para poder afrontar trabajos de mecanizado con ciertas garantías.

■ Uso de plataformas libres

Crucial si se requiere reducir el precio al máximo exponente. De este modo se puede tener acceso a software gratuito y hardware a un precio mínimo, que además no solamente resulta beneficioso desde un punto de vista económico, ya que es reconfortante saber que el proyecto está respaldado por una gran comunidad que presta ayuda totalmente desinteresada, cegados quizás por la total pasión por las cosas que hacen.

■ Obtención del diseño de la fresadora mediante software CAD

Para ello se ha empleado el software de diseño SolidWorks 2012 y para el diseño de plantillas o aspectos más específicos la versión de estudiante de AutoCAD 2011.

Es interesante que probablemente se ha dedicado más tiempo al diseño del dispositivo sobre el ordenador que realmente en el taller, pero los beneficios de realizarlo así han permitido una ejecución limpia, donde la mayoría de los problemas se habían detectado a priori en el ordenador, y no después.

Este flujo de trabajo, resulta inevitable en la actualidad, ya que los proyectos de ingeniería han alcanzando una complejidad tal que es inconcebible realizarlos sin antes disponer de la seguridad de un diseño en ordenador, junto con simulaciones y todos los parámetros que aseguren su correcto funcionamiento.

■ Fabricación de la estructura mecánica de la fresadora en DM

Se ha optado principalmente por el uso de paneles de madera de densidad media, o DM (Densidad media) ya que ofrecen un gran rendimiento a un precio más que ajustado. De esta forma se asegura un coste final mucho más reducido al empleo de elementos metálicos, con una repercusión de calidad estructural mínima.

■ Diseño e implementación del sistema de control CNC de tres ejes

Actualmente, la tecnología de CNC está tremendamente extendida, dejando cada vez más fuera de lugar a los métodos artesanos. Su proliferación ya llevado a que no solo grandes empresas dispongan de ellos, sino más bien, que se trate de un estándar dentro del taller.

Si se analizan los elementos de cualquier CNC, todos radican en una estructura muy similar. La principal diferencia entre ellos son el número de ejes, la capacidad o no de cambio de herramienta y la sensorización.

El llevado a cabo en este proyecto cumple con el siguiente:

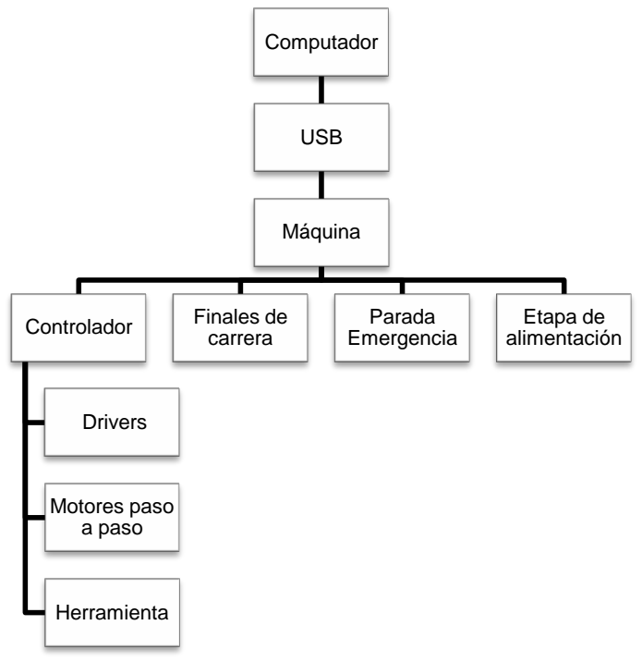
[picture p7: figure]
Computador; USB; Máquina; Controlador; Drivers; Motores paso a paso; Herramienta; Finales de carrera; Parada Emergencia; Etapa de alimentación

Ilustración 1. Esquema CNC

De nuevo, el controlador empleado debe de cumplir la premisa de bajo coste. Existen multitud de soluciones, pero la más interesante es sin duda el uso de Arduino. La transparencia de los proyectos con Arduino, así como la gran comunidad que hay detrás apoyándolos lo convierten en idóneo. Más adelante se dedicará un capítulo exclusivamente a este dispositivo.

■ Obtención de piezas mecanizadas

Este proyecto resultaría vacío si tras ejecutarlo, no se demostrase el correcto funcionamiento del conjunto mediante el mecanizado de piezas de ejemplo. Obviamente hay que asumir una serie de compromisos en el diseño de la máquina y en lo que es capaz de trabajar, pero realmente el objetivo no es obtener piezas de extrema calidad dimensional en materiales como acero o aluminio.

El objetivo es comprender los fundamentos y a aplicarlos sobre materiales no muy complejos de mecanizar, como maderas, plásticos, papel o el mecanizado de cobre sobre baquelita para crear placas de circuito impreso.

## 2. INTRODUCCIÓN

## 2.1 Fabricación de PCB’s

Un circuito impreso o PCB (Printed Circuit Board), es una tarjeta o placa utilizada para realizar el emplazamiento de los distintos elementos que conforman el circuito y las interconexiones eléctricas entre ellos.

Antiguamente era habitual la fabricación de circuitos impresos para el diseño de sistemas mediante técnicas caseras, sin embargo esta práctica ha ido disminuyendo con el tiempo. En los últimos años el tamaño de las componentes electrónicas se ha reducido en forma considerable, lo que implica menor separación entre pines para circuitos integrados de alta densidad. Teniendo también en consideración las actuales frecuencias de operación de los dispositivos, es necesaria una muy buena precisión en el proceso de impresión de la placa con la finalidad de garantizar tolerancias mínimas.

Los circuitos impresos más sencillos corresponden a los que contienen caminos de cobre (tracks o pistas) solamente por una de las superficies de la placa. A estas placas se les conoce como circuitos impresos de una capa, o en inglés, One layer PCB.

Los circuitos impresos más comunes de hoy en día son los de 2 capas o two layers PCB, aprovechando así las dos caras de cobre que puede disponer una placa.

Este nivel de precisión y miniaturización, acompañados de una feroz demanda así como un aumento en estándares de calidad, ha exigido a la industria desarrollar métodos fiables y muy avanzados para cumplir las necesidades. Así pues, dependiendo de la complejidad del diseño del físico del circuito pueden llegar a fabricarse placas con hasta 8 o más layers.

En la siguiente figura se pueden apreciar tres configuraciones de PCB, una a dos capas, otra a cuatro y otra a seis. El espesor de los circuitos impresos puede variar dependiendo de la aplicación, sin embargo la más utilizada es 1.6mm.

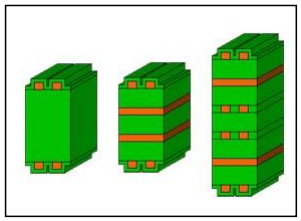
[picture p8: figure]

Ilustración 2. Capas de un circuito impreso

Aunque existen multitud de formas para fabricar estas placas, a nivel industrial las más aceptadas y desarrolladas son mediante insolación y atacado químico para la producción en masa y el mecanizado mediante fresadora para la producción de prototipos o diseños con series muy pequeñas.

### 2.1.1 Fabricación mediante insolación

Cualquier diseño de una placa de circuito impreso parte de un diseño en ordenador de un esquemático. Desde este esquemático, se generan las pistas, vías y se distribuyen sobre la superficie buscando el máximo ahorro, optimizando el espacio. Sobre este diseño, se imprime en un fotolito el diseño. Este fotolito se trata del “molde”.

Mediante serigrafía se reproduce en las placas de cobre el diseño, como si de una fotografía se tratase. Es decir, en primer lugar se insolan las placas de cobre cubiertas con un barniz reactivo a la luz y protegidas por el fotolito. El fotolito logra que se generen sombras en aquellos puntos en los que hay cobre, es decir, tracks.

Hecho esto, se insertan las placas de cobre en una mezcla reveladora, que eliminará el barniz sobrante y las dejará listas para el atacado químico. El atacado elimina el cobre de aquellas partes que previamente fueron insoladas, preservándose las que recibieron sombra.

Aunque parezca un proceso agresivo, y desgraciadamente contaminante por la gran cantidad de residuos que se generan, la precisión que se obtiene así como la capacidad de producción en masa ha hecho que se trate del método optado por los fabricantes de electrónica de consumo.

Para producir placas con multitud de capas, se insola cada capa y tras realizar el conexionado de ellas, se inserta el conjunto en una prensa obteniendo un bloque compacto.

### 2.1.2 Fabricación mediante mecanizado

Este proceso como ya se ha anticipado principalmente se emplea para realizar prototipos de una forma rápida y limpia.

Tras el diseño de la PCB desde un ordenador, no se imprime el fotolito, sino que se genera el gerber o fichero de control numérico que suele ser a una o dos capas. Una máquina provista de una fresa o conjunto de fresas de precisión se encarga de interpretar el fichero y mecanizar mediante eliminación de material la placa de circuito impreso.

Este proceso es mucho más cómodo que el anterior y permite obtener diseños de forma más rápida que el anterior, pero obviamente, cuando se trata de producción en masa, este método supone un cuello de botella.

Este método para obtener diseños de forma rápida ha sido la fuente de inspiración de este proyecto. Así pues, todo el desarrollo que sigue consiste en crear un dispositivo de control numérico capaz de crear diseños mediante arranque de material.

## 2.2 Control numérico

Resulta interesante introducir el concepto de control numérico. Se trata de una máquina capaz de realizar multitud de tareas y que ha sido el fundamento de los sistemas robóticos más avanzados de la actualidad.

La máquina herramienta ha jugado un papel fundamental en el desarrollo tecnológico del mundo hasta el punto que no es descabellado afirmar que la tasa del desarrollo de máquinas herramientas gobierna directamente la tasa del desarrollo industrial.

Surge y se desarrolla a lo largo del tiempo por la exigencia de cubrir ciertas necesidades: necesidad de fabricar productos que no se podían conseguir en cantidad y calidad suficientes sin recurrir a la automatización del proceso de fabricación, necesidad de obtener productos hasta entonces imposibles o muy difíciles de fabricar, por ser excesivamente complejos para ser controlados por un operador humano, necesidad de fabricar productos con unos costes de producción suficientemente bajos, etc.

Inicialmente, el factor predominante que condicionó todo automatismo fue el aumento de la productividad. Posteriormente, debido a las nuevas necesidades de la industria aparecieron otros factores no menos importantes como la precisión, la rapidez y la flexibilidad.

Las siglas CNC hacen referencia a Control Numérico Computerizado. Básicamente se trata del control automatizado de una máquina herramienta para la realización de determinados trabajos mecánicos.

El origen del CNC se encuentra sobre los años 50. El primer CNC real se desarrolló por la industria aeronáutica para la realización de mecanizados complejos que requerían de interpolación entre ejes para conseguir superficies complejas tridimensionales.

El funcionamiento básico de una maquinaria de control numérico incluye los siguientes aspectos:

■ | En una máquina CNC, a diferencia de una máquina convencional o manual, una
| computadora controla la posición y velocidad de los motores que accionan varios ejes
| de la máquina. Gracias a esto, puede hacer movimientos que no se pueden lograr
| manualmente como círculos, líneas diagonales o figuras complejas tridimensionales.
■ | Las máquinas CNC son capaces de mover la herramienta al mismo tiempo en los tres
| ejes para ejecutar trayectorias multidimensionales como las que se requieren para el
| mecanizado de moldes complejos y troqueles.
■ | En una máquina CNC una computadora controla el movimiento de la mesa, el carro y el
| husillo. Una vez programada la máquina, ésta ejecuta todas las operaciones por sí
| sola, sin necesidad de que el operador esté manejándola. Esto permite aprovechar
| mejor el tiempo del personal.

Al mismo tiempo que se han desarrollado los sistemas CNC han evolucionado los sistemas de CAD/CAM. CAD/CAM es el proceso mediante el cual se utilizan las computadoras para mejorar la fabricación, y diseñar los productos. Éstos pueden fabricarse de forma más rápida, más precisa o con unos costes de fabricación menores, con la aplicación adecuada de tecnología informática.

Los sistemas CAD (acrónimo de Computer Aided Design) son sistemas de Diseño Asistido por Ordenador, éstos pueden utilizarse para generar modelos con muchas, si no todas, de las características de un determinado producto. Estas características podrían ser el tamaño, el contorno y la forma de cada componente, almacenados como dibujos bidimensionales y/o tridimensionales. Una vez que estos datos dimensionales han sido introducidos y almacenados en el sistema informático, el diseñador puede manipularlos o modificar las ideas del diseño con mayor facilidad para avanzar en el desarrollo del producto. Además, pueden compartirse e integrarse las ideas combinadas de varios diseñadores, ya que es posible mover los datos dentro de redes informáticas, con lo que los diseñadores e ingenieros situados en lugares distantes entre sí pueden trabajar como un equipo. Los sistemas CAD también permiten simular el funcionamiento de un producto. Hacen posible verificar si un circuito electrónico propuesto funcionará tal y como está previsto, si un puente será capaz de soportar las cargas pronosticadas sin peligros e incluso si una salsa de tomate fluirá adecuadamente desde un envase de nuevo diseño.

Cuando los sistemas CAD se conectan a equipos de fabricación también controlados por ordenador conforman un sistema integrado CAD/CAM (CAM, acrónimo de Computer Aided Manufacturing o Fabricación Asistida por ordenador). Este flujo de trabajo gráficamente es:

La Fabricación Asistida por Ordenador ofrece significativas ventajas con respecto a los métodos más tradicionales al controlar equipos de fabricación con ordenadores en lugar de hacerlo con operadores humanos.

En los inicios del CNC hacer un programa de mecanizado era muy difícil y tedioso, pues había que planear e indicarle manualmente a la máquina cada uno de los movimientos que tenía que hacer. Era un proceso que podía durar horas, días, semanas. Aún así era un ahorro de tiempo comparado con los métodos convencionales.

También se emplean sistemas CAD/CAM para generar el programa de mecanizado de forma automática. En el sistema CAD (diseño asistido por ordenador) la pieza que se desea maquinar se diseña en la computadora con herramientas de dibujo y modelado sólido. Posteriormente el sistema CAM (fabricación asistida por ordenador) toma la información del diseño y genera la ruta de corte que tiene que seguir la herramienta para fabricar la pieza deseada; a partir de esta ruta de corte se crea automáticamente el programa de mecanizado, el cual puede ser introducido a la máquina mediante un disco o enviado electrónicamente.

A la hora de implementar un dispositivo de control numérico, existen multitud de soluciones pero que en general todas cumplen con la siguiente estructura:

Computador

Interfase

Controlador

Drivers

Motores

Herramienta

Finales de
carrera

Otra
sensorización

### 2.2.1 Interfase máquina – ordenador

Se trata del programa encargado de mostrar información sobre el estado de la máquina en una pantalla, así como permitir una comunicación bidireccional entre ambos. Existen multitud de soluciones. La más famosa es sin duda Mach3 (Mach4 actualmente en desarrollo) totalmente compatible con cualquier versión desde Windows 2000. Para usuarios de Linux la más recomendable es EMC2, proyecto totalmente “Open Source”, aunque existen otras muchas como KCAM, solución perfecta para usuarios de Windows 98.

La solución optada en este proyecto es GRBL, otro trabajo totalmente Open Source optimizado para trabajar sobre Arduino, soportado por una comunidad muy preparada que lo mejora día a día. Los autores de este software lo definen como:

“Grbl is an opensource software that turns your Arduino development board into a full blown G-Code interpreter.”

Para comunicar el controlador con el ordenador se ha optado por GRBL Controller 3.6.1, un software libre y gratuito producido por el maravilloso autor de Zapmaker.org. El programa puede ser descargado gratuitamente desde esa misma web. Su interfaz es la siguiente:

Ilustración 3. Interfaz de GRBL Controller

### 2.2.2 Controlador

El uso de GRBL implica directamente a Arduino, en concreto se recomienda el uso de Arduino UNO Rev3.

Arduino es una plataforma de electrónica abierta para la creación de prototipos basada en software y hardware flexibles y fáciles de usar. Se creó para artistas, diseñadores, aficionados y cualquiera interesado en crear entornos u objetos interactivos.

El microcontrolador en la placa Arduino se programa mediante el lenguaje de programación Arduino (basado en Wiring) y el entorno de desarrollo Arduino (basado en Processing). Los proyectos hechos con Arduino pueden ejecutarse sin necesidad de conectar a un ordenador, si bien tienen la posibilidad de hacerlo y comunicar con diferentes tipos de software (p.ej. Flash, Processing, MaxMSP).

Las placas pueden ser hechas a mano o compradas montadas de fábrica; el software puede ser descargado de forma gratuita. Los ficheros de diseño de referencia (CAD) están disponibles bajo una licencia abierta.

Existen multitud de tarjetas Arduino, cada una con unas características determinadas que las hacen idóneas para una aplicación u otra. En este proyecto, se ha empleado probablemente la tarjeta más genérica, Arduino UNO Rev3.

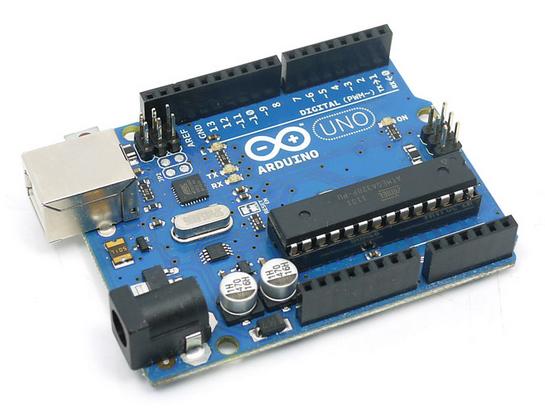
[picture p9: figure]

Ilustración 4. Arduino UNO Rev3

Arduino UNO es una placa basada en el microcontrolador ATmega328. Principalmente dispone de 14 pines digitales de entrada/salida (de los cuales 6 se pueden utilizar como salidas PWM (pulse-width modulation)), 6 salidas analógicas, un reloj de 16MHz y un puerto USB. La placa dispone de todo lo necesario para hacer funcionar el microcontrolador, por lo que su uso resulta tremendamente sencillo.

Otra funcionalidad interesante que llevó a su uso, es que aunque la tarjeta funcione por puerto serial, realmente lo emula desde un puerto USB, por lo que se puede manejar desde cualquier portátil. No es necesario el uso de grandes torres con puerto serial.

Sus principales características técnicas son:

Microcontrolador | ATmega328
Voltaje de operación | 5V
Tensión de entrada | 7-12V
Límite tensión de entrada | 6-20V
Pines digitales E/S | 14 (6 PWM)
Pines analógicos entrada | 6
Corriente pin E/S | 40mA
Corriente pin 3.3V | 50mA
Memoria flash | 32 KB (0.5KB bootloader)
SRAM | 2 KB
EEPROM | 1 KB
Frecuencia de reloj | 16 MHz

Hay muchos otros microcontroladores y plataformas con microcontroladores disponibles para la computación física. Parallax Basic Stamp, BX-24 de Netmedia, Phidgets, Handyboard del MIT, y muchos otros ofrecen funcionalidades similares. Todas estas herramientas organizan el complicado trabajo de programar un microcontrolador en paquetes fáciles de usar. Arduino, además de simplificar el proceso de trabajar con microcontroladores, ofrece algunas ventajas respecto a otros sistemas a profesores, estudiantes y amateurs:

■ | Asequible: las placas Arduino son más asequibles comparadas con otras
| plataformas de microcontroladores.
■ | Multi-Plataforma: el software de Arduino funciona en los sistemas operativos
| Windows, Macintosh OSX y Linux. La mayoría de los entornos para
| microcontroladores están limitados a Windows.
■ | Entorno de programación simple y directo: el entorno de programación de Arduino
| es fácil de usar para principiantes y lo suficientemente flexible para los usuarios
| avanzados.
■ | Software ampliable y de código abierto: el software Arduino está publicado bajo
| una licencia libre y está preparado para ser ampliado por programadores
| experimentados. El lenguaje puede ampliarse a través de librerías de C++, y si se
| está interesado en profundizar en los detalles técnicos, se puede dar el salto a la
| programación en el lenguaje AVR C en el que está basado. De igual modo se
| puede añadir directamente código en AVR C a los programas.
■ | Hardware ampliable y de Código abierto: Arduino está basado en los
| microcontroladores ATMEGA168, ATMEGA328 yATMEGA1280. Los planos de los
| módulos están publicados bajo licencia Creative Commons, por lo que
| diseñadores de circuitos con experiencia pueden hacer su propia versión del
| módulo, ampliándolo u optimizándolo.

Existen tres tipos de memoria en los microcontroladores utilizados por las placas Arduino (ATmega168, ATmega328, ATmega1280, etc.): memoria Flash, memoria SRAM y memoria EEPROM. A continuación se indican las diferencias de cada una de ellas y el uso que Arduino puede darles.

La memoria Flash (espacio del programa) es donde Arduino almacena el sketch. Un sketch es el nombre que usa Arduino para un programa. Es la unidad de código que se sube y ejecuta en la placa Arduino. Esta memoria es no volátil, si Arduino deja de ser alimentado eléctricamente los datos que haya en esta memoria permanecerán.

El tamaño de la memoria Flash de Arduino puede variar dependiendo del microcontrolador, aunque no es muy grande. Por ejemplo, para el chip ATmega168 el tamaño de la memoria Flash es de 16 kilobytes, de los cuales 2 kilobytes son utilizados por el bootloader. Para el caso del microcontrolador ATmega328 (como el que incorpora Arduino UNO) el tamaño de la memoria Flash es de 32KB, de los cuales el bootloader usa 0,5KB. Por lo que se debe desarrollar los programas de forma muy optimizada.

La memoria SRAM (Static Random Access Memory ó memoria estática de acceso aleatorio) es de tipo volátil, es el espacio donde los sketches (programas) almacenan y manipulan variables al ejecutarse. La información guardada en esta memoria será eliminada cuando Arduino pierda la alimentación. Esta memoria es de uso exclusivo para el programa en ejecución.

La memoria SRAM de Arduino es muy pequeña, por lo que se debe optimizar los programas al máximo y no abusar de variables de tipo char muy grandes. Hay que tener en cuenta que cada carácter de una variable char utiliza un byte. En el microcontrolador ATmega 168 el tamaño de la memoria SRAM es de 1024 bytes, para el caso de un chip ATmega328 (como el que incorpora Arduino UNO) el tamaño es de 2KB (2048 bytes).

Si la SRAM se queda sin espacio, el programa de Arduino fallará de forma imprevista, aunque se compile y se suba a Arduino correctamente la aplicación no se ejecutará o se ejecutara de manera extraña.

EEPROM es un espacio de memoria que puede ser utilizado por los programadores para almacenar información a largo plazo. Este tipo de memoria es no volátil, por lo que los datos guardados en ella permanecerán aunque Arduino pierda la alimentación. Esta memoria puede ser usada para guardar valores si es necesario.

El tamaño de la EEPROM para un chip ATmega128 es de 512 bytes, para un chip ATmega328 es de 1KB (1024 bytes). Hay que tener en cuenta que el tamaño de la memoria EEPROM interna de Arduino es "pequeño" pero Arduino admite añadir módulos de memoria EEPROM externa de mayor tamaño.

Cabe destacar, que la memoria EEPROM en general soporta hasta 100000 ciclos de guardado. Tras superarlos, la memoria puede dejar de funcionar en cualquier momento.

Las funcionalidades de esta placa se pueden incrementar exponencialmente mediante el uso de shields (anglicismo ampliamente utilizado en este argot). Son placas que pueden ser conectadas encima de la placa Arduino extendiendo sus capacidades. Las diferentes shields siguen la misma filosofía que el conjunto original: son fáciles de montar y baratos de producir.

Ilustración 5. Arduino UNO con shield

Aunque en realidad existen shields de todo tipo para realizar tareas específicas, los más importantes son:

■ | Conexión Wi-fi.
■ | Conexión Ethernet y módulo SD.
■ | Soporte para display.
■ | Driver para motores de continua o paso a paso.
■ | Para el prototipado.

En la ejecución de este proyecto se va a emplear un shield específico para GRBL, del que más adelante se profundizará en todos los detalles.

El lenguaje de programación de Arduino es una implementación de Wiring, una plataforma de computación física parecida, que a su vez se basa en Processing, un entorno de programación multimedia. En realidad, es muy similar a C++.

Para realizar el programa, es obligatorio emplear al menos las dos siguientes funciones:

void setup(){
//Se ejecuta una vez, cuando se inicia el sketch. //Corresponde a la etapa de configuración del programa. }

void loop(){
//Se ejecuta de forma continua. Contiene el programa //principal.
}

El programa es insertado a la placa a través de un cable USB que actúa como puerto serial. Para ello, se requiere del IDE que se puede descargar gratuitamente desde la página oficial de Arduino. A su vez, este IDE contiene los drivers de la placa, por lo que la configuración es muy sencilla.

El programa de GRBL que va a correr sobre Arduino consiste en un sketch que se carga sobre el ATmega328 y permite a Arduino interpretar el código G y enviar las señales de control a los drivers. Está especialmente diseñado para trabajar sobre la placa UNO, aunque también se puede adaptar sobre otras que dispongan del microprocesador ATmega328. GRBL no es autónomo, es decir, requiere de un software adicional que envíe a Arduino el código G, del que más adelante se hablará. Debido a la limitada memoria de Arduino UNO, GRBL permite interpretar la mayoría de operaciones que generan los programas CAM, no obstante, no es excesivamente bueno interpretando código realizado por “humanos” ya que no soporta estructuras de control, variables ni funciones. No permite instalar un display por lo que la comunicación se realiza mediante comandos.

Existen diferentes revisiones de GRBL. Si se desea descarga la penúltima revisión (0.8c, la empleada en este proyecto), basta con ir al siguiente enlace:

https://github.com/grbl/grbl/downloads

Existe una versión más actualizada pero que aún se encuentra en fase beta y de la que se conoce poco. Los autores afirman que utilizan un algoritmo para los drivers más suave y rápido. Además, trabaja hasta a 30kHz, pero puesto que aún se trata de una beta y contiene pequeños errores que se irán depurando con el paso del tiempo, se ha preferido emplear una versión más fiable en este proyecto.

### 2.2.3 Drivers

Existen infinidad de posibles soluciones para controlar los motores. De entre todas las posibles soluciones, y debido a la arquitectura del shield de GRBL (más adelante se detallará), quedan todas descartadas excepto una, el driver Pololu A4988. Aunque si bien es cierto que esto ha simplificado la tarea de elegir el driver, la máxima intensidad que admite limita en cierta manera los motores a emplear. No obstante, el resultado, como más adelante se verá, es más que satisfactorio para las dimensiones de esta máquina.

En concreto, se ha empleado la revisión BLACK del A4988, que tiene el siguiente aspecto:

Ilustración 6. Driver Pololu A4988 BLACK

Se trata de un driver de sencillo uso preparado para trabajar con motores paso a paso bipolares. Incluye un potenciómetro que permite regular la intensidad de salida hasta los 2A por bobina. Sus principales características son:

Tensión entrada motor | 8-35V
Tensión entrada lógica | 3.3-5V
Corriente de salida | 1A (Hasta 2A con disipador)
Temperatura ambiente | -20-85°C
Resolución máxima | 1/16

Los pines de que dispone son:

Ilustración 7. Pines driver Pololu A4988

■ | VDD: Entrada de tensión entre 3.3 y 5V. Alimentación de la etapa lógica.
■ | VMOT: Entrada de tensión entre 7-12V. Alimentación de los motores.
■ | DIR: dirección de sentido de giro del motor.
■ | STEP: cuando se produce un cambio de nivel bajo a nivel alto provoca un giro de
| un paso sobre el motor.
■ | SLP (activo a nivel bajo): pone al driver en modo de bajo consumo.
■ | RST (activo a nivel bajo): Todas las entradas de STEP se ignoran mientras este
| pin esté a nivel alto.
■ | EN: driver encendido cuando la entrada está conectada a masa. Driver apagado
| cuando se encuentra a nivel alto
■ | MS1, MS2 y MS3: necesarios para los micropasos, hasta una resolución de 1/16.

MS0 | MS1 | MS2 | RESOLUCIÓN
BAJO | BAJO | BAJO | 1
ALTO | BAJO | BAJO | 1/2
BAJO | ALTO | BAJO | 1/4
ALTO | ALTO | BAJO | 1/8
ALTO | ALTO | ALTO | 1/16

Aunque el driver está preparado para trabajar sobre motores bipolares, también es posible hacerlo funcionar sobre motores unipolares. El conexionado es el siguiente:

Bipolar 4 conductores | Unipolar 6 conductores

Es importante definir el tiempo que deben de durar los pulsos para que realmente funcione el driver correctamente. De la hoja de características del fabricante (datasheet) se puede obtener la siguiente información, crucial para que el motor funcione correctamente:

Ilustración 8. Ancho de pulso driver Pololu A4988

STEP mínimo, ALTO | 1μs
STEP mínimo, BAJO | 1μs
Corriente de salida | 200ns
Tensión de entrada | 200ns

Por lo que, a nivel de programación en Arduino, un código adecuado para hacer girar sin ningún problema un motor de 200 pasos por vuelta a velocidad constante es:

#define DIR 3

#define STEP 6

#define RST 9

void setup(){
pinMode(STEP,OUTPUT);
pinMode(DIR,OUTPUT);
pinMode(RST,OUTPUT);
digitalWrite(RST,LOW);
}

void loop () {
for(int i=0;i<200;i++) {
digitalWrite(STEP,LOW);
delayMicroseconds(30);
digitalWrite(STEP,HIGH);
delay(1);
}
}

Actualmente ha aparecido una revisión de este driver, llamada DRV8825, con exactamente el mismo conexionado. En un futuro, o en un proyecto similar, se emplearía esta nueva versión. Sus principales características son las siguientes:

Tensión entrada motor | 8.2-45V
Tensión entrada lógica | 3.3-5V
Corriente de salida | 1.5A (Hasta 2.2A con disipador)
Temperatura ambiente | -20-85°C
Resolución máxima | 1/32

Presenta el siguiente aspecto:

Ilustración 9. Driver Pololu DRV8825

### 2.2.4 Motores

Los motores eléctricos más comunes empleados en este tipo de proyectos son:

■ Motor de continua: se compone principalmente de dos partes. El estator da soporte mecánico al aparato y contiene los devanados principales de la máquina, conocidos también con el nombre de polos, que pueden ser de imanes permanentes o devanados con hilo de cobre sobre núcleo de hierro. El rotor es generalmente de forma cilíndrica, también devanado y con núcleo, alimentado con corriente directa mediante escobillas fijas (conocidas también como carbones). El principal inconveniente de estas máquinas es el mantenimiento, muy caro y laborioso, debido principalmente al desgaste que sufren las escobillas al entrar en contacto con las delgas.
■ | Motor | sin | escobillas | (brushless): | es | un motor | eléctrico que | no
emplea escobillas para realizar el cambio de polaridad en el rotor. Esto aumenta enormemente su durabilidad.
■ Motor paso a paso: es un dispositivo electromecánico que convierte una serie de impulsos eléctricos en desplazamientos angulares discretos, lo que significa que es capaz de avanzar una serie de grados (paso) dependiendo de sus entradas de
| control.

En las MHCN más simples con prestaciones basadas en la precisión del mecanizado se utilizan los motores paso a paso como actuadores primarios. Con motores de este tipo, el giro se subdivide en incrementos fijos que son controlados mediante un número de pulsos dado. Sin embargo cuando se desean trabajos pesados de mecanizado con pares resistentes elevados durante el frenado o aceleración, su fiabilidad y prestaciones disminuye. El uso de motores de este tipo está restringido a pares resistentes bajos.

Para este proyecto, no cabe duda de que el motor más adecuado es el paso a paso. Su facilidad de uso, su robustez y su gran precisión los hacen idóneos para aplicaciones de precisión. Su principal inconveniente es que para su excitación requieren de una etapa lógica, denominada driver. Su principal característica es el hecho de poder moverlos un paso a la vez por cada pulso que se les aplique. Este paso puede variar desde 90° hasta pequeños movimientos de centésimas de grado. Un motor que gire 1.8° por cada pulso, necesitará de 200 pulsos para efectuar una vuelta completa. Otras características son:

■ | Posibilidad de estacionamiento en determinados puntos de su giro dependiendo
| de la amplitud del paso, es decir, su resolución.
■ | Aplicación de par en situación estacionaria.
■ | Alta precisión en el posicionamiento con un error que oscila entre un 3 y un 5% de
| la longitud del paso, no acumulable entre un paso y el siguiente.
■ | Posee numerosas ventajas sobre los motores convencionales: los únicos
| elementos de rozamiento son los rodamientos (no posee escobillas), el coste del
| control es menor, se le pueden aplicar muy bajas velocidades de giro sin pérdida
| del par, poseen una mayor amplitud de velocidades de giro efectivas y poseen una
| mejor respuesta a las señales que se le envían.

Para este proyecto, la única limitación en cuanto al motor a emplear es que su consumo nominal no sea mayor de 2A por bobina. De entre todas las posibilidades, el que más se ajusta es sin duda el motor NEMA 23 de 14Kg/cm. El motor, con un diseño robusto y contundente, se muestra en la siguiente fotografía extraída de la web del fabricante:

Ilustración 10. NEMA 23

Sus principales características son:

Ángulo de paso | 1.8 grados
Pasos | 200 pasos/vuelta
Fases | 4
Voltaje | 4.5V
Corriente | 2A/fase
Diámetro del eje | 6.35mm
Par | 14Kg/cm
Formato | NEMA 23

Se trata de un motor unipolar de 6 hilos, por lo que para conectarlo al driver las líneas amarilla y blanca se deben de dejar sin conectar, como anteriormente se ha indicado.

### 2.2.5 Mecánica del CNC

En general, la estructura de los controles numéricos se suele realizar en perfilería de aluminio, dado lo sencillo que es trabajarlo y los excelentes resultados que ofrece en cuanto a precisión, resistencia y durabilidad. No obstante, en la ejecución de este proyecto se ha optado principalmente al uso de tableros de densidad media (DM) con densidad de 750Kg/m³
. Un tablero de DM es un aglomerado elaborado con fibras de aglutinadas con resinas sintéticas mediante fuerte presión y calor, en seco, hasta alcanzar una densidad media. Empleando así piezas de acero y APM para los sistemas de transmisión y otros elementos mecánicos.

Se ha optado por emplear este material principalmente por la disponibilidad tanto de la materia prima como de herramientas para trabajar madera. El resultado, no debe de tener nada que envidiar al uso de aluminio, aunque eso sí, requerirá de cierto trabajo extra.

Los recorridos de la herramienta en el seno de la pieza se originan por la acción combinada de los desplazamientos en cada uno de sus ejes principales.

Los sistemas de transmisión producen traslaciones rectilíneas en los ejes principales a partir del giro básico generado por el grupo del motor-reductor.

El corazón del movimiento de las MHCN es la transmisión por recirculación de bolas. Consiste en un sinfín acanalado y un acoplamiento al que se fija el conjunto mecánico a desplazar. Cuando el grupo del motor gira, su rotación se transmite al husillo y el cuerpo del acoplamiento se traslada longitudinalmente a través de este arrastrando consigo a la mesa de trabajo en el sentido oportuno.

El accionamiento contiene un conjunto de bolas en recirculación que garantizan la transmisión de esfuerzos del sinfín a la mesa con unas pérdidas por fricción mínimas. Las dos partes de su cuerpo están ajustadas con una precarga para reducir al mínimo el juego transversal entre ellas con lo que se mejora la exactitud y repetitibilidad de los desplazamientos.

Para disminuir los daños del mecanismo de transmisión frente a colisiones transversales o sobrecargas, el grupo motriz puede incorporar un embrague en su conexión con el sinfín. Este dispositivo desacopla la transmisión cuando el conjunto de la mesa choca contra algún obstáculo.

Los desplazamientos longitudinales de los ejes no deben ser afectados, en la medida de lo posible, por los esfuerzos y acciones exteriores (por ejemplo las fuerzas de corte). Por esta razón es esencial que los sistemas de transmisión y guía garanticen la rigidez mecánica.

Adicionalmente la transmisión debe producir movimientos suaves y estables y ser capaz de reaccionar rápidamente en las aceleraciones y deceleraciones.

Para este proyecto, no se han empleado husillos de gran calidad, ni transmisión por recirculación, ya que el coste del conjunto se incrementaría enormemente. En vez de esto, se ha utilizado un tornillo sin fin con rosca M12 y paso 1mm, transmitiendo el movimiento lineal a una tuerca con una arandela soldada para permitir su sujeción al elemento a desplazar. Todo esto se aclarará más adelante.

### 2.2.6 Control de la posición

Para obtener la máxima precisión, los controles numéricos profesionales disponen de sensorización en los ejes como encoders para conocer la posición exacta de la herramienta. Se trata de un sistema de realimentación que le otorga a la máquina “ojos” y permite posicionar sean cuales sean las circunstancias la máquina en el punto adecuado.

Esta se trata de la estructura más típica de un lazo de control en regulación automática:

Un sistema en lazo abierto no recibe información acerca del estado de la máquina, simplemente ejecuta una acción suponiendo de antemano cuales van a ser las consecuencias. Dada su sencillez esta va a ser la estructura llevada a cabo en este proyecto, y realmente va a ser válida, pues son pocos los factores que pueden interferir en el libre desplazamiento de la transmisión. Quizás el uso de una herramienta muy desgastada que ofrezca una desorbitada oposición, pero en este caso, verdaderamente el problema no es que la máquina este realimentada o no, es el lamentable estado de la fresa.

## 3. DESARROLLO

Con el fin de organizar el proyecto, la información se mostrará en orden cronológico a como se ha realizado, pudiendo dividirla en: programación del microcontrolador (Arduino), etapa de electrónica y potencia, fabricación de la estructura e implementación eléctrica y configuración de GRBL Controller.

## 3.1 Programación de Arduino

El sketch introducido en la placa Arduino es la versión 0.8c de GRBL, ya que su funcionamiento está totalmente garantizado.

Se puede acceder a la configuración de GRBL en el fichero Config.h desde el IDE de Arduino. La empleada en este proyecto ha sido:

#define STEPPERS_DISABLE_DDR | | DDRB

#define STEPPERS_DISABLE_PORT | | PORTB

#define STEPPERS_DISABLE_BIT | | 0

#define STEPPERS_ENABLE_DDR | DDRB

#define STEPPERS_ENABLE_PORT | PORTB

#define STEPPERS_ENABLE_BIT | 0

#define STEPPERS_ENABLE_VAL | 0 | // 0=low 1=high

#define STEPPING_DDR | DDRD

#define STEPPING_PORT | PORTD

#define X_STEP_BIT | 2

#define Y_STEP_BIT | 4

#define Z_STEP_BIT | 6

#define X_DIRECTION_BIT | 3

#define Y_DIRECTION_BIT | 5

#define Z_DIRECTION_BIT | 7

#define LIMIT_DDR | DDRB

#define LIMIT_PIN | PINB

#define X_LIMIT_BIT | 1

#define Y_LIMIT_BIT | 4

#define Z_LIMIT_BIT | 5

#define SPINDLE_ENABLE_DDR DDRB #define SPINDLE_ENABLE_PORT PORTB #define SPINDLE_ENABLE_BIT 2

#define SPINDLE_DIRECTION_DDR DDRB #define SPINDLE_DIRECTION_PORT PORTB #define SPINDLE_DIRECTION_BIT 3

Esta configuración no es trivial y más a delante se detallará el principal motivo por el que se ha elegido: adaptar la tarjeta de Arduino al shield específico de GRBL. A continuación se muestra una leyenda gráfica de los pines anteriormente configurados:

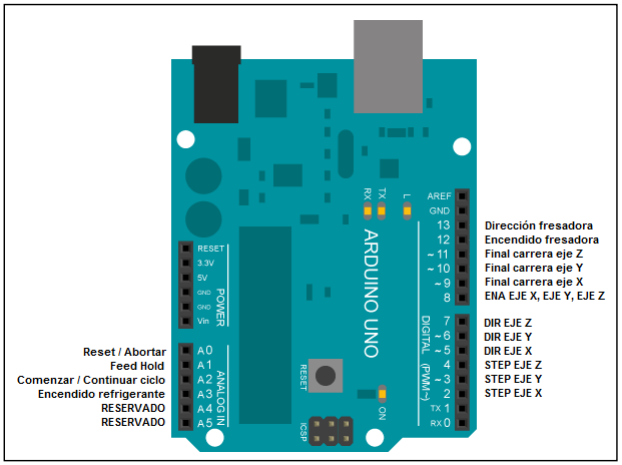
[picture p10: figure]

Ilustración 11. Conexionado GRBL

Como se puede apreciar, los drivers que soporta son los que disponen de señales STEP, DIR y ENABLE. Es importante destacar que los pines de ENABLE de todos los drivers son comunes y se conectan al pin 8 de Arduino.

Este conexionado abarca todos los pines de que dispone el Arduino UNO. Obviamente los pines 1 y 2 correspondientes a transmisión Tx y Rx no se pueden emplear ya que Arduino está en todo momento comunicándose por el puerto serial. Los pines A4 y A5 están reservados y probablemente se les añada en un futuro nuevas funcionalidades.

Existen multitud de formas de conexionado de los drivers. Una de ellas es conectar directamente los drivers de forma individual, como pueden ser los EasyDriver V4.4.

Ilustración 12. Conexión EasyDriver

También se puede optar por conectar un sistema de control de motores embebido en una PCB, como pueden ser los proyectos de synthetos.com (grblShield o TinyG), pero lo más recomendable, y lo realizado en este proyecto ha sido el uso de un shield específicamente diseñado para GRBL. De este modo, se aprovechan todas las funcionalidades tanto de GRBL como de los drivers de una forma muy compacta. Más adelante se detallarán los aspectos de este shield.

### 3.1.1 Instalación del Sketch de GRBL para Windows

El programa, o sketch de GRBL se encuentra dentro de un fichero hexadecimal, por lo que no se puede introducir directamente desde el IDE de Arduino al microcontrolador. Para realizarlo correctamente, se debe de utilizar un programa específico para flashear sobre el microcontrolador el firmware. En este proyecto, se ha empleado XLoader v1.00. No obstante, hay que tener presente que antes de flashear Arduino, los drivers de Arduino UNO tienen que estar instalados. Cuando se ejecuta XLoader, la pantalla se debe de configurar de la siguiente forma:

Ilustración 13. XLoader v1.00

■ | Hex file: directorio donde se encuentra el archivo de código fuente de GRBL en
| hexadecimal.
■ | Device: GRBL solamente es compatible con el microcontrolador ATmega 328. Se
| recomienda flashear únicamente Arduino UNO, que obviamente dispone de este
| microcontrolador.
■ | COM port: puerto donde está conectada la tarjeta de Arduino.
■ | Baud rate: se recomienda una velocidad de 115200, de forma que la transferencia
| sea lo más rápida posible.

Una vez configurada la ventana, se hace click en “Upload”. Si el puerto está correctamente seleccionado GRBL comenzará a volcarse en la tarjeta y comenzará a parpadear. Una vez finalizado este proceso, XLoader no volverá a hacer falta.

Es importante destacar que si el shield de GRBL se encuentra conectado a la tarjeta Arduino este proceso no se puede llevar a cabo, ya que los pines 0 y 1 (Tx y Rx) se deben de encontrar libres cuando se programa la tarjeta desde el ordenador.

## 3.2 Etapa de electrónica y potencia

Una vez que se tiene el controlador programado, es momento de ubicar todos los drivers y demás partes eléctricas.

### 3.2.1 GRBL Shield

Con GRBL cargado, ya se está en condición de implementar a nivel de hardware el conexionado de los drivers con el controlador. Tras probar las diferentes posibilidades, la solución óptima ha resultado en adquirir un shield específicamente diseñado para GRBL con el fin de lograr un dispositivo compacto y facilitar el conexionado.

Se trata de un diseño hardware libre elaborado por Bertus Kruger de Protoneer. Existen diferentes versiones, la usada en este proyecto es la 3.00, que tiene este aspecto:

Ilustración 14. Shield GRBL

GRBL solamente es compatible con controles numéricos de 3 ejes, por lo que el cuarto driver se puede emplear para duplicar la fuerza motriz en un eje. En este proyecto no se ha considerado necesario, por lo que solo se hace uso de 3 drivers.

En el siguiente esquemático se pueden observar todos los pines.

Ilustración 15. Esquemático shield GRBL

Teóricamente la placa está diseñada para trabajar con hasta 36V, pero hay que llevar cuidado ya que si los drivers no están preparados para soportar esta alimentación serán destruidos cuando se alimente. En este trabajo se han empleado los POLOLU A4988, fijando la alimentación en 12V.

La forma de configurar algunos parámetros de la placa es mediante el uso de jumpers y no mediante programación. En concreto, los jumpers son empleados para configurar el uso del cuarto eje (duplicación de un eje ya existente para aumentar la potencia motriz), micropasos de los drivers y los finales de carrera.

Configuración de los micropasos

Cada eje puede ser configurado mediante diferentes micropasos. Es recomendable que todos los ejes tengan la misma configuración. Los jumpers deben de ser situados en las siguientes posiciones:

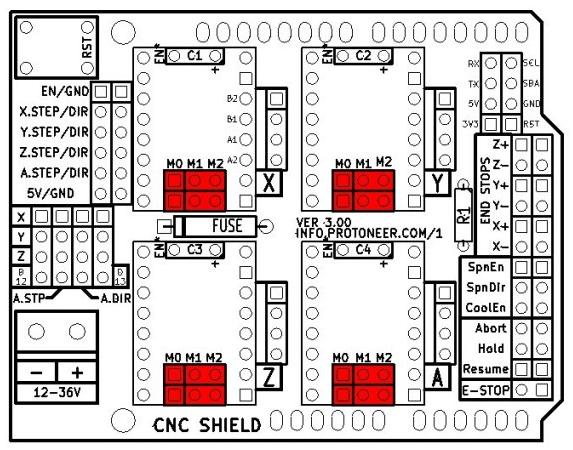
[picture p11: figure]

Ilustración 16. Configuración micropasos shield GRBL

La siguiente tabla muestra la configuración para el driver Pololu A4988:

MS0 | MS1 | MS2 | RESOLUCIÓN
BAJO | BAJO | BAJO | 1
ALTO | BAJO | BAJO | 1/2
BAJO | ALTO | BAJO | 1/4
ALTO | ALTO | BAJO | 1/8
ALTO | ALTO | ALTO | 1/16

La siguiente tabla muestra la configuración para el driver Pololu DRV8825:

MS0 | MS1 | MS2 | RESOLUCIÓN
BAJO | BAJO | BAJO | 1
ALTO | BAJO | BAJO | 1/2
BAJO | ALTO | BAJO | 1/4
ALTO | ALTO | BAJO | 1/8
BAJO | BAJO | ALTO | 1/16
ALTO | BAJO | ALTO | 1/32
BAJO | ALTO | ALTO | 1/32
ALTO | ALTO | ALTO | 1/32

Configuración del cuarto eje

Usando dos jumpers se puede clonar el eje X, Y o Z. Realmente también se puede usar como un eje independiente usando el pin digital 12 como STEP y el pin digital 12 como DIR, pero GRBL no soporta más que 3 ejes.

Cuarto eje como eje X

Ilustración 17. Cuarto eje como eje X

Cuarto eje como eje Y

Ilustración 18. Cuarto eje como eje Y

Cuarto eje como eje Z

Ilustración 19. Cuarto eje como eje Z

Cuarto eje controlado por los pines 12 y 13

Ilustración 20. Cuarto eje controlado por los pines 12 y 13

Configuración de los finales de carrera

Por defecto, GRBL está configurado para recibir alertas cuando la entrada de los finales de carrera se referencia a masa.

Ilustración 21. Final de carrera normalmente abierto

Esto realmente es peligroso. Supongamos que el cable del final de carrera se rompe o simplemente está averiado. Aunque la máquina llegue a una posición extrema, nunca se va a parar, pues esta configuración de contacto normalmente abierto va a seguir indicando a GRBL que todo funciona correctamente.

El conexionado detallado de los finales de carrera conectados directamente a la tarjeta Arduino con resistencias de pull-up para mantener la entrada a nivel alto es el siguiente:

Ilustración 22. Conexionado detallado de los finales de carrera

El conexionado de los finales de carrera se simplifica mediante el empleo del shield de GRBL, ya que no requiere del uso de resistencias de pull-up externas, siendo simplemente necesario conectar el final de carrera normalmente abierto a los pines específicos. Además, se ha realizado una revisión al shield, con versión 3.02 que permite emplear o finales de carrera normalmente abiertos o normalmente cerrados, solucionando el problema de seguridad anteriormente citado.

Ilustración 23. Configuración final de carrera shield GRBL

Si el jumper está situado en la posición izquierda entonces el final de carrera se considerará que está activo cuando se referencia a masa. Si está situado a la derecha, se considera que está referenciado a Vcc.

Desgraciadamente en la redacción de este proyecto no se ha contado con esta revisión de la placa, por lo que los finales de carrera, aunque son totalmente funcionales, requieren de un mantenimiento periódico para asegurar que funcionan correctamente y evitar problemas.

En concreto, se han situado seis finales de carrera, suficientes para asegurar un funcionamiento seguro de la máquina en su funcionamiento automático (y manual).

Otras funcionalidades

Además de la configuración del cuarto eje, el uso de micropasos y los finales de carrera, este shield dispone de otras funcionalidades, de las que cabe citar:

■ | Señal de activación de relé para activar la herramienta mediante el comando M3 y
| M5.
■ | Señal para establecer un sentido u otro para el giro de la herramienta.
■ | Activación o desactivación de suministro de refrigerante.
■ | Pin para abortar el proceso (parada de emergencia).

■ | Pin para pausar el proceso.
■ | Pin para continuar el proceso.

Los diseñadores han “sacado” una gran cantidad de pines con el fin de explotar al máximo las capacidades de Arduino. Se dispone de salida de 5V y 3.3V (obviamente con las limitaciones de potencia que puede otorgar el regulador de Arduino UNO), pines Rx, Tx para comunicación por el puerto serie, SCL y SDA para comunicación mediante el protocolo I²C, además de pines para estimular externamente las entradas DIR y STEP de los drivers. Por último, cabe destacar que aún se ha conservado el botón de reset.

De todas estas funcionalidades extra, la única verdaderamente útil es el uso de una seta de emergencia. Está directamente conectada en paralelo al pin reset de Arduino, por lo que al accionarla, se produce una “parada lógica” y no un corte de alimentación. Dicho de otro modo, cuando Arduino se reinicia, GRBL se reinicializa, parando todos los motores y desactivando el relé de la fresadora. La parada segura está asegurada.

### 3.2.2 Drivers

Ubicar los drivers es una tarea realmente sencilla, simplemente hay que conectarlos con los pines adecuadamente.

El driver presenta un potenciómetro que permite regular la intensidad que suministra a cada bobina. La forma hacer esto no resulta sencilla y por eso se ha considerado necesario aclarar cómo hacerlo en este documento. En primer lugar hay que observar un terminal relativamente escondido:

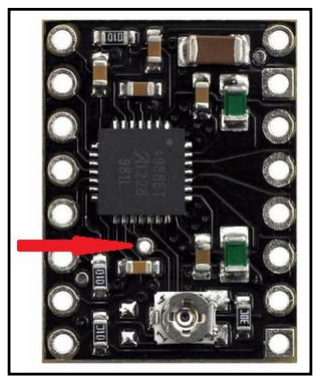
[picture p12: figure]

Ilustración 24. Detalle pin Vref A4988

Se trata del pin Vref. Para ajustar la intensidad, hay que medir la tensión que hay entre este pin y masa, y aplicar la siguiente fórmula:

En este proyecto, y como se verá más adelante, se ha llevado el driver al máximo, extrayendo de él 2A, por lo que en el terminal Vref se debe de medir 0.8V. Obviamente, en estas circunstancias, ha sido fundamental dotar de disipador al driver. Además, y debido a la cercanía de los tres drivers, se ha dotado de un sistema de refrigeración activa mediante ventilador. Más adelante se detallará el mecanismo de extracción de calor.

### 3.2.3 Motores

El conexionado de los motores Nema 23 también resulta sencillo, pero hay que tener en cuenta un aspecto que puede llevar a confusión, ya que el autor del shield de GRBL no utiliza la misma nomenclatura en los nombres de los cables que en los drivers. Es decir, en vez de usar B2, B1, A1, A2, hay que usar 2B, 2A, 1A, 1B, donde:

2B | Rojo
2A | Azul
1A | Verde
1B | Negro

Aunque en este momento presentar este apartado pueda resultar precipitado (más adelante se hablará sobre los parámetros constructivos de la máquina), es necesario para llegar a entender la precisión que dota el conjunto de motor paso a paso y tornillo roscado.

El desplazamiento angular del motor se traduce en un desplazamiento lineal de la herramienta mediante el husillo. Esto proporciona una gran precisión así como una gran potencia en el desplazamiento. Como principal inconveniente, la velocidad lineal se ve enormemente atenuada, la cual depende obviamente de la velocidad de giro del motor, pero también del paso de la rosca.

Los tornillos empleados son de paso 1mm. No se ha empleado un paso mayor con el fin de no comprometer la precisión de la máquina. Esto significa que por cada vuelta completa que efectúe el motor, el eje se desplazará 1mm. Dicho de otra forma:

Los motores empleados requieren de 200 pulsos para efectuar una vuelta completa, por lo que por cada pulso el eje girará 1.8°, luego la velocidad angular viene determinada por:

Donde f representa la frecuencia del tren de pulsos.

Esta relación se puede observar gráficamente:

También se puede expresar en términos de periodo:

Esta última expresión, permite calcular sencillamente la velocidad angular a partir del tiempo entre pulso y pulso (T) del motor paso a paso.

Aclarado esto, cabe destacar que los motores paso a paso presentan una limitación en cuanto a la frecuencia de los pulsos, tanto como si es muy elevada como si es muy baja. La máxima frecuencia admisible suele estar alrededor de los 625 Hz, en caso de que la frecuencia de pulsos sea demasiado elevada, el motor puede reaccionar en alguna de las siguientes maneras:

■ | No realizar ningún movimiento en absoluto.
■ | Comenzar a vibrar pero sin llegar a girar.
■ | Girar erráticamente.
■ | Girar en sentido opuesto.
■ | Perder potencia.

Personalmente, para la configuración de NEMA 23 y tornillo sin fin de paso 1mm, la máxima velocidad de desplazamiento se encuentra, como mucho, en 280mm/min. El resultado no es tan elevado como se hubiera deseado. En un futuro, se podrían sustituir los tornillos sin fin por otros de paso 2mm o incluso 4mm, aumentando enormemente la velocidad de desplazamiento lineal, aunque infiriendo ligeramente de forma negativa en la precisión y en el par máximo.

### 3.2.4 Accionamiento de la fresadora

Una solución posible a la hora de realizar un trabajo es presionar el botón de encendido de la fresadora y apagarla manualmente cuando el proceso termina, pero la idea es automatizar el sistema lo máximo posible. Mediante las funciones de control numérico M3 y M5 se puede actuar sobre un pin digital de Arduino para encender y apagar la herramienta. Esto, además de aumentar la comodidad, permite ahorrar energía en movimientos rápidos sobre la pieza, apagando la máquina, así como otorgando robustez en los ciclos de mecanizado.

Desgraciadamente, no se puede controlar automáticamente la velocidad de giro de la herramienta, ya que dispone de un potenciómetro que se debe de accionar físicamente. Por suerte, la mayoría de trabajos se pueden realizar a la máxima velocidad de giro, por lo que no será necesario de modificar constantemente, salvo cuando se busque la máxima precisión y rendimiento.

Al usar como herramienta la fresadora, existe un problema de incompatibilidad de potencia en la señal de control. Arduino proporciona 5V, mientras que la fresadora funciona a 230. En este instante están coincidiendo la etapa de control y la de potencia. Para efectuar este nexo, la solución inmediata es el uso de un relé.

El relé es un dispositivo electromecánico. Funciona como un interruptor controlado por un circuito eléctrico en el que, por medio de una bobina y un electroimán, se acciona un juego de uno o varios contactos que permiten abrir o cerrar otros circuitos eléctricos independientes.

Dado que el relé es capaz de controlar un circuito de salida de mayor potencia que el de entrada, puede considerarse, en un amplio sentido, como un amplificador eléctrico.

La gran ventaja de los relés electromagnéticos es la completa separación eléctrica entre la corriente de accionamiento, la que circula por la bobina del electroimán, y los circuitos controlados por los contactos, lo que hace que se puedan manejar altos voltajes o elevadas potencias con pequeñas tensiones de control. También ofrecen la posibilidad de control de un dispositivo a distancia mediante el uso de pequeñas señales de control.

Para este proyecto, se ha optado por emplear un módulo de relé comercial que incluye toda la etapa de acondicionamiento, que principalmente se trata de un diodo que permite la libre circulación de corriente en el bobinado del relé cuando la señal de control desaparece (de este modo se evitan posibles y peligrosas fugas de corriente hacia el controlador), así como un transistor para aumentar la ganancia de la intensidad.

Ilustración 25. Relé fresadora

Sus principales características son:

Señal de control | 3.5-12V
Salida | N.C. y N.A.
Señal de potencia | VDC (30V) y VAC (250V)
Dimensiones | 40x27x18mm

Por seguridad, cabe destacar un importante fallo de diseño que tiene este relé. Al otro lado de la PCB, están las soldaduras. Las más grandes son las correspondientes a la regleta de tres terminales para conectar la alimentación de la herramienta. No es difícil, si se está manipulando el relé mientras está conectado, poner las manos sobre estas soldaduras que están a 230V. Es necesario situar el relé sobre una base segura que no permita en ningún momento acceder con las manos a la parte trasera de la PCB.

### 3.2.5 Alimentación

Para alimentar todo el conjunto se ha optado por emplear una fuente de alimentación de ordenador de tipo ATX. Esta solución es perfecta ya que a un precio muy razonable, se disponen de multitud de salidas a diferente tensión y además se dispone de ventilador para contribuir a la refrigeración de los drivers.

En concreto se ha empleado el modelo TMXPT0500 de TECNIMAX, que ofrece hasta una potencia de 500W, y además ofrece protección frente a sobrecarga y cortocircuito, perfecto para las primeras fases de la ejecución del proyecto. Esta se encarga de alimentar el shield de GRBL (los drivers), el ventilador y el relé. La alimentación de la fresadora se hace directamente a 230V.

Sus principales características son:

Tensión de entrada | 230VAC
Frecuencia de entrada | 50Hz
Eficiencia | >70% a plena carga
Temperatura de funcionamiento | 0-40⁰C
Protecciones | OVP (Sobrevoltaje) OCP (Sobretensión) SCP (Cortocircuito)

Como toda fuente de alimentación de estas características, ofrece las siguientes salidas:

Naranja | 3.3V
Rojo | 5V
Amarillo | 12V
Azul | -12V
Violeta | VSB 5V
Negro | GND

El esquema eléctrico de todas las conexiones antes de la etapa de la fuente de alimentación es:

Tras la fuente de alimentación, no ha sido necesario emplear todas las salidas que dispone la fuente ATX. A continuación se muestran las usadas:

GRBL Shield + | 12V
GRBL Shield - | GND
Ventilador + | 12V
Ventilador - | GND
Relé + | 5V
Relé - | GND

Este montaje se puede observar de una forma más clara, y aplicada, en la siguiente fotografía extraída directamente desde la máquina:

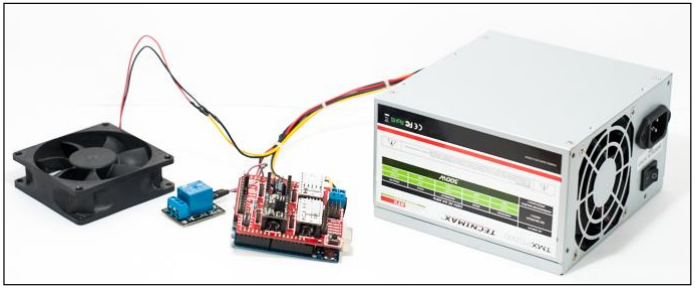
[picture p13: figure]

Ilustración 26. Conexiones fuente de alimentación

Esta imagen contiene mucha información. Además de observar las conexiones desde la fuente de alimentación, se puede apreciar el Arduino UNO soportando el shield GRBL con tres drivers, el relé, y el ventilador. A falta de los finales de carrera, y de la seta de emergencia, contiene toda la parte de control del CNC. Aunque dos drivers son de color blanco y otro de color negro, ambos corresponden a la versión BLACK de los A4988. La única diferencia, es que se adquirieron desde otro proveedor y parece que no se pusieron de acuerdo con el color de la máscara de soldadura.

Obsérvese el detalle del interruptor de la fuente de alimentación. Permite apagar fácilmente el CNC sin necesidad de desconectar ningún cable.

Todo este conjunto, montado sobre una plataforma de DM de 10mm para otorgarle robustez, tiene el siguiente aspecto:

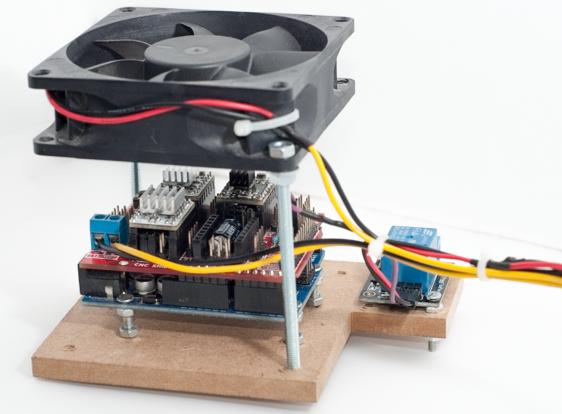
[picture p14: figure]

Ilustración 27. Bloque controlador

El shield sobre Arduino no es capaz de alimentar al microcontrolador, por lo que este aunque sea alimentado, Arduino requiere también de alimentación externa. La solución es más que sencilla ya que se alimenta directamente desde el puerto USB.

Por ello, para que la máquina funcione, debe de estar conectada permanentemente al ordenador.

### 3.2.6 Disipación del calor

Motores y drivers son sinónimo de calor. En este proyecto, donde todo el sistema electrónico va a estar embebido en una caja cerrada y donde se van a efectuar largos ciclos de mecanizado, es crucial planificar e idear un método para la correcta refrigeración del sistema.

Ya se han presentado los dos ventiladores que van a contribuir a la ventilación forzada. Aunque no es objetivo de este apartado presentar la estructura mecánica, es necesario adelantar una imagen para entender mejor el sentido de caudal de aire que se pretende conseguir con la disposición de los ventiladores.

La entrada de aire la produce el ventilador situado sobre los drivers. En concreto, se trata de un ventilador de 70mm con un consumo de intensidad de 0.15 amperios con una tensión de 12 voltios. Este ventilador proporciona un caudal muy similar al que dispone la fuente de alimentación, uno de 80mm, que se encarga de expulsar el aire por el lazo izquierdo.

Sobre los drivers, tal y como recomienda el fabricante, se han situado disipadores de aluminio de 13x13x7 milímetros con un adhesivo termoconductor.

Ilustración 29. Detalle disipador driver

Los resultados de este conjunto han sido excepcionales, tras periodos de mecanizado de 120 minutos, no se ha apreciado en ningún momento un calentamiento notable.

### 3.2.7 Interferencias electromagnéticas

Algunos usuarios de GRBL han tenido dificultades con este al quedar constantemente congelado mientras se estaba enviando el código G. Esto no es un problema del software, sino más bien del entorno. Este problema se produce por las interferencias electromagnéticas que producen los dispositivos de alta potencia, como por ejemplo, los cables de la fresadora.

Para evitar esto, todo el cableado va a ser ordenado, empleando un cable USB blindado y dispuesto lo más lejos posible de todas las fuentes de ruido electromagnético.

### 3.2.8 Finales de carrera

Simplemente se han empleado seis finales de carrera accionados mecánicamente con configuración normalmente abierta (NA), empleando los pines X+, X-, Y+, Y-, Z+ y Z- de GRBL Shield.

Ilustración 30. Final de carrera

Su disposición aunque pueda parecer obvia, no está de mal incluirla en este documento, con el fin de describir con todo detalle el ensamblaje. El único factor que se ha tenido en cuenta para elegir el modelo del final de carrera es que tuviera un tamaño adecuado que resultara cómodo para colocarlo, y sobretodo que fuera muy robusto, de forma que si por cualquier motivo o despiste la máquina no se detenga al final de la carrera (inadecuada configuración del software de control), no lo destroce, si no que más bien, detenga por la fuerza a la máquina. Teniendo todo esto en cuenta, el empleado ha sido un interruptor muy genérico de la marca RJ. Sus especificaciones técnicas no tienen ningún interés.

Como cualquier otro interruptor de este tipo, dispone de una salida normalmente abierta y otra normalmente cerrada. Sus dimensiones sin incluir los terminales son 28x16x10mm. Se ubica con dos tornillos de diámetro 3mm. Sin ánimo de adelantar el diseño estructural de la máquina, su disposición es la siguiente:

Ilustración 31. Disposición final de carrera Z- y Z+

Ilustración 32. Disposición final de carrera X- y X+

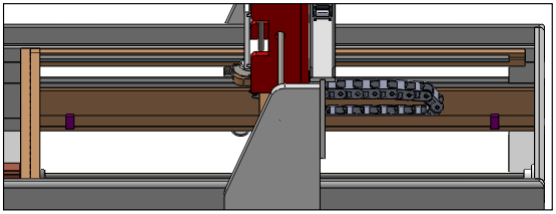
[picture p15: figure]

Ilustración 33. Disposición final de carrera Y- e Y+

### 3.2.9 Parada de emergencia

Se ha empleado una seta de emergencia con configuración normalmente abierta (NA), empleando el pin E-Stop de GRBL Shield. Estará situada en una zona perfectamente accesible.

## 3.3 Estructura y cableado

El software CAD se ha convertido en una herramienta informática de vital importancia para la ingeniería. Conocer a priori los aspectos fundamentales de un diseño, sin necesidad de perder tiempo en el taller con el famoso método de ensayo y error ni dinero en material, es fundamental.

El diseño de la máquina ha sido minuciosamente creado desde SolidWorks 2012, con el fin de simplificar el trabajo en el taller. Las piezas más comprometidas, han sido creadas desde una plantilla impresa a escala 1:1. Algunos planos de detalle han requerido del uso de AutoCAD 2011 con el fin de concretar detalles. El resultado, ocultando las tapas para no perder detalle, es el siguiente:

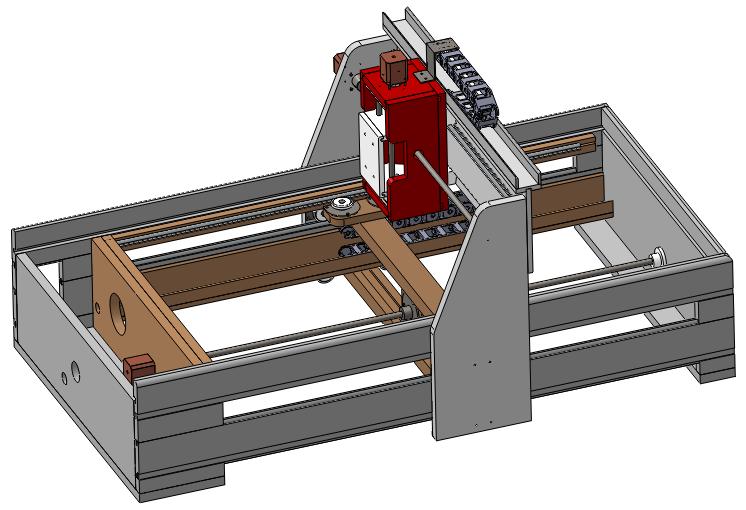
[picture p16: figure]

Ilustración 34. Ensamblaje completo de la máquina

Este diseño no solo contiene información estructural. Si no también de acabado superficial con la pintura, así como parámetros físicos como densidad de los materiales para obtener el peso total del ensamblaje, siendo teóricamente 38.3 kilogramos, a lo que habrá que añadir el peso de la electrónica y de la herramienta, por lo que probablemente la máquina finalmente termine pesando algo más de 40 kilogramos. Sus dimensiones son 1190x638x590mm.

Por motivos de tiempo, no se ha incluido el cableado ni los dispositivos electrónicos, aunque sí todos los orificios para ubicarlos.
El diseño prácticamente se ha hecho en madera de densidad media (DM) con ρ=750kg/m³ aproximadamente. Otras tantas, se han mecanizado en acero.

Cualquier pieza de las fotografías es fiel al diseño en SolidWorks, por lo que si se requiere de alguna cota, se recomienda recurrir al anejo de planos.

### 3.3.1 Sistema de transmisión

La solución óptima habría sido emplear husillos calibrados, pero debido a su elevado precio, se ha optado por emplear varillas roscadas de acero de rosca M12 con un paso de 1mm. Las ventajas que habría presentado el uso de husillo son las siguientes:

■ | Filetes más gruesos, por lo que la durabilidad es mayor.
■ | Mayor paso de rosca. Esto permite una velocidad más elevada de
| desplazamiento.
■ | Debido al ángulo de las crestas de la rosca, la fuerza aplicada en el husillo es
| mayor, pero en la varilla roscada al ser el paso menor esta fuerza se compensa.
■ | Mayor precisión (muchísima).

No obstante, el resultado con las varillas roscadas ha sido más que aceptable. Desde el inicio del proyecto se han sacrificado ciertos aspectos de precisión con el fin de hacer la máquina rentable económicamente. Además, como también se indicó, el objetivo es conocer los fundamentos de los dispositivos CNC, no lograr mecanizar piezas con tolerancias dimensionales y geométricas de micras. El conjunto de transmisión se muestra a continuación, aunque obviamente en la máquina se han empleado varillas roscadas de mayor longitud. Este sistema se ha triplicado a lo largo de los tres ejes.

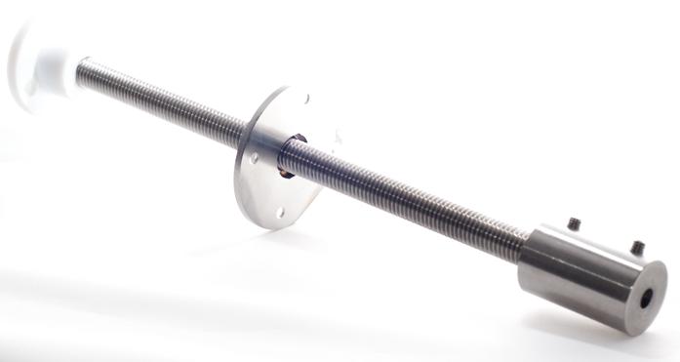
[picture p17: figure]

Ilustración 35. Sistema de transmisión

En esta imagen se pueden apreciar las cuatro piezas para el sistema de transmisión. La primera se trata de un casquillo mecanizado mediante torno para unir el eje del motor con el tornillo. Además, dispone de dos pequeños prisioneros para asegurar la integridad del conjunto y un correcto acoplamiento. De nuevo, al realizar esta pieza se asumen ciertas pérdidas de precisión al no emplear casquillos flexibles.

Ilustración 36. Casquillo de motores

Como ya se ha dicho, el tornillo roscado es de M12 con un paso de 1mm. La velocidad máxima que se puede obtener ya ha sido analizada en apartados anteriores, y aunque a priori pueda parecer lenta, ha resultado ser eficaz. Para mejorar el funcionamiento y evitar problemas de desgaste prematuras, habrá que lubricar adecuadamente los tornillos.

El final del tornillo es una pieza mecanizada en Celotex. Este material presenta una durabilidad excelente frente al desgaste. El alojamiento para el tornillo presenta algo de juego para poder absorber los movimientos sobre el plano de giro del tornillo.

Ilustración 37. Tope varilla roscada

Antes de mecanizar estos topes con un ligero juego en el alojamiento del tornillo, se soldó una arandela a un cojinete y se mecanizó el eje hembra interior para poder atornillar el sin fin, anulando cualquier juego posible. El resultado fue un completo desastre, ya que en vez de aumentar la suavidad del conjunto, se produjo el efecto contrario. Las desviaciones en los tornillos sin fin hacían que resultada imposible hacerlo girar al no disponer de ningún grado de libertad.

Por último, la pieza que se acopla al bloque que se pretende desplazar es simplemente una tuerza de acero con una chapa de acero solada, rectificada mediante torno en una de sus caras para asegurar la máxima precisión.

Ilustración 38. Tuerca de transmisión

Con esta pieza se han aceptado de nuevo muchos compromisos de calidad. Este sistema de tuerca no asegura que no se pierdan pasos debido al juego de la tuerca con respecto al tornillo sin fin cuando se efectúan cambios de sentido en el movimiento. Este fenómeno de juego mecánico se llama backlash.

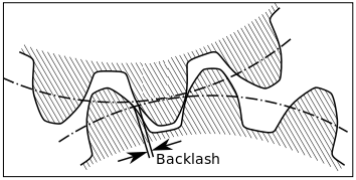
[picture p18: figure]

Ilustración 39. Backlash

Finalizado este estudio del sistema de transmisión de la máquina, se procede a explicar las tres partes fundamentales de la estructura: la base, el carro y la cabeza, así como sus correspondientes métodos de ensamblaje.

### 3.3.2 Sistema de soporte y deslizamiento

Independientemente del sistema de transmisión, las partes móviles de la máquina deben de deslizar con precisión y de forma suave por las guías. Inicialmente se pensó en el empleo de ejes calibrados de acero o guías lineales, pero debido al elevado precio, se han optado por otras opciones más acordes a obtener un coste final adecuado.

Puesto que se ha empleado un mecanismo diferente para cada eje, se ha incluido en los siguientes apartados una explicación de cómo se ha llevado a cabo el sistema de deslizamiento.

### 3.3.3 Base (eje y)

El tamaño máximo de la máquina ha estado determinado por la longitud máxima de las varillas roscadas que es de un metro (1000mm). Esa es la longitud de la varilla que se ha empleado en el eje y. Hablando de ejes, conviene definir el sistema de coordenadas cartesianas que va a tener esta máquina.

Ilustración 40. S.C. de la máquina

Luego es adecuado llamar la base como eje y, el brazo o puente como eje x y la cabeza como eje z.

Se ha optado por hacer la base con un perfil bajo a la que se le suplementarán caballetes metálicos para elevar la máquina. Este ensamblaje dispone de un alojamiento tanto para la electrónica como un pequeño espacio para poder guardar herramientas de demás útiles. De esta forma el motor motriz del eje y queda oculto. Todas las piezas se han mecanizado en DM.

El aspecto en SolidWorks es el siguiente:

Ilustración 41. Vista de perfil de la base

Ilustración 42. Vista delantera de la base

Ilustración 43. Vista superior de la base

Ilustración 44. Vista isométrica de la base

Esta parte de la máquina tiene unas dimensiones de 1160x638x257mm. Sin contar con el peso de la electrónica (el motor sí está incluido), pero sí con las dos tapas superiores, el programa de CAD arroja un valor de peso de 22.6 kilogramos. Este elevado peso le otorgará una gran robustez al conjunto.

La lista de piezas es la siguiente:

Nombre de la pieza | Cantidad | Masa
Tapadera grande | 1 | 4645,23
Delante con guía | 1 | 1981,31
Atrás sin guía | 1 | 1592,12
Base grande | 1 | 1545,56
Atrás interior | 1 | 1531,28
Lateral inferior derecho | 1 | 1261,99
Lateral superior | 2 | 1208,44
Lateral inferior | 1 | 1198,37
Tapadera pequeña | 1 | 790,5

Base pequeño | 1 | 636,4
Base soporte cadena porta cables | 1 | 375,21
Limite tapadera pequeña | 1 | 324,9
Guía suplemento | 2 | 324,06
Guía aluminio | 6 | 248,9
Base lateral cadena porta cables ancha | 1 | 219,22
Apoyo tapadera grande | 1 | 162,45
Casquillo | 1 | 143,69
Tope grande superior derecho | 1 | 126,48
Base lateral cadena porta cables | 1 | 87,84
Tope grande superior | 1 | 86,2
Tope grande inferior derecho | 1 | 75,35
Tope grande inferior | 1 | 67,57
Motor Nema 23 | 1 | 1012,28
Tope pequeño superior | 2 | 52,08
Tope pequeño inferior | 2 | 31,03
Apoyo tornillo sin fin baquelita | 1 | 15,34
Tornillo (M3 x0.5x25) | 4 | 0,22
Arandela | 4 | 0,04

Esta lista de piezas no incluye toda la tornillería necesaria para ensamblar las piezas.

El sistema de unión con el brazo se ha realizado mediante una solución relativamente original, empleando ruedas calibradas y un sistema de guías de aluminio.

Ilustración 45. Rueda transmisión

En SolidWorks tiene este aspecto:

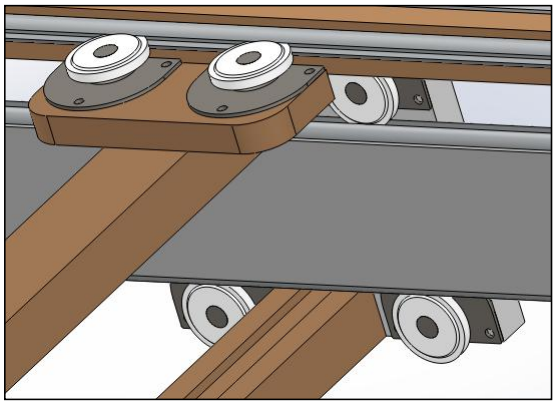
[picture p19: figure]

Ilustración 46. Unión base y brazo

Las ruedas verticales superiores soportan tanto el peso del brazo como de la cabeza. Las situadas en la parte inferior realmente no tienen ninguna tarea comprometida. Simplemente evitar que el carro pueda salir de las guías. La pareja de ruedas horizontales, se ha situado para evitar movimientos flectores del carro que principalmente ocurren cuando la herramienta penetra en el material:

Ilustración 47. Evitando movimiento flector del carro

El conjunto se comporta muy bien, mostrando un aspecto robusto. Existen unas pequeñas holguras, pero puesto que realmente el junto va a trabajar a compresión el comportamiento general ha sido más que satisfactorio.

### 3.3.4 Puente (eje x)

Esta es probablemente la parte más sencilla del ensamblaje. Este puente contiene la motorización para el eje x, así como soporte para el eje z. Presenta la siguiente vista isométrica:

Ilustración 48. Vista isométrica brazo

Esta parte de la máquina tiene unas dimensiones de 676x190x525mm. Sin contar con el peso de la electrónica (el motor sí está incluido), el programa de CAD arroja un peso de 8.08 kilogramos.

La lista de piezas es la siguiente:

Nombre de archivo | Cantidad | Masa
Apoyo tornillo sin fin baquelita | 1 | 15,34
Brazo base cadena porta cables | 1 | 228,07
Brazo derecho | 1 | 1109,99
Brazo izquierdo | 1 | 1101,47
Brazo lateral cadena porta cables | 2 | 60,11
Brazo transmisión | 1 | 205,92
Casquillo | 1 | 143,69
Guía aluminio corta | 2 | 167,15
Motor Nema 23 | 1 | 721,39
Tornillo M3 x 0.5 x 30 | 4 | 0,26
Rueda guía | 12 | 7,78
Soporte eje X | 1 | 145,25
Soporte guía corta | 1 | 689,04
Soporte rueda guía | 12 | 60,21
Soporte ruedas suplemento | 2 | 96,94
Tapa eje X | 1 | 912,6
Unión brazos | 2 | 672,29

La pieza más comprometida de este ensamblaje es el segmento de DM que se va a encargar de soportar el peso de la cabeza (Soporte eje X). Está reforzado por detrás por otro rectángulo de DM de 10mm (Tapa eje X), que además de otorgar robustez, contendrá el canal para la cadena portacables. De hecho, antes de acoplar este refuerzo, se observó como a medida que pasaron los días esta pieza se torsionó ligeramente aun estando atornillada, simplemente debido al peso de la cabeza.

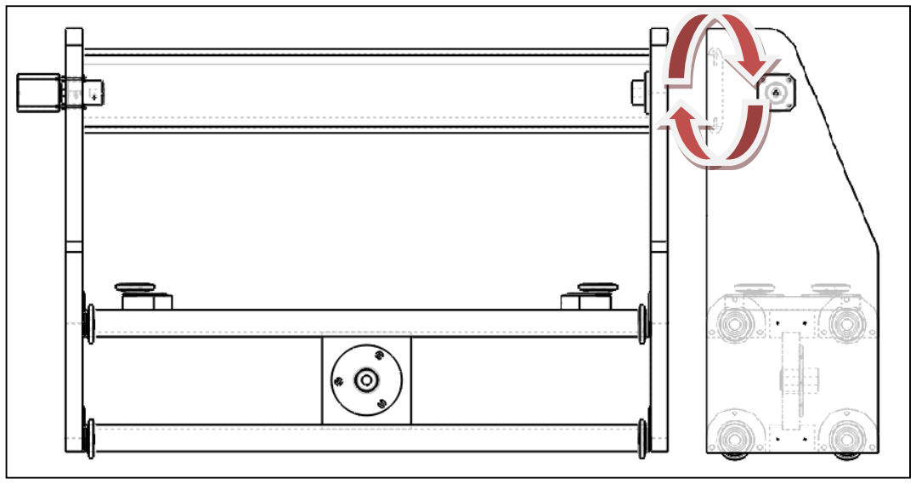
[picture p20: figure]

Ilustración 49. Deformación de la pieza “Soporte eje X” sin refuerzo

Para soportar la cabeza, y permitir que esta deslice a lo largo del eje X, de nuevo se ha optado por emplear guías de aluminio. No obstante, dada la precisión que debe de tener el conjunto, no se han acoplado a la cabeza ruedas, si no que se han mecanizado unas piezas en APM a medida para que el juego sea mínimo. A diferencia del sistema de guías entre la base y el brazo que trabajaban simplemente a compresión, la cabeza recibirá esfuerzos flectores sobre todo cuando la herramienta penetre en el material.

Ilustración 50. Soporte cabeza

Se emplearán dos piezas como ésta situadas en la cabeza. Una en la parte inferior, y otra en la parte superior, de forma que se van a requerir de nuevo dos guías de aluminio.

### 3.3.5 Cabeza (eje z)

Esta ha sido la parte más compleja de fabricar. Realmente toda la estructura radica en este punto. Aquí es donde radica la precisión de la máquina. Debido al poco espacio de trabajo dentro de esta pieza, en el diseño se tuvo muy en cuenta como poder realizar el ensamblaje. A continuación se muestra su aspecto final.

Ilustración 51. Vista isométrica cabeza

Este ensamblaje tiene unas dimensiones de 115x142x310mm, con un peso total de 3.3 kilogramos (ni herramienta ni soporte de herramienta incluidos).

El sistema de deslizamiento sobre el eje Z se puede entender como dos cajas, la externa, inmóvil, y la interna, la cual desliza a través de tres redondos calibrados de acero de diámetro 10mm. Esta última pieza se ha realizado en APM debido a sus ventajosas propiedades de deslizamiento y durabilidad. A continuación se muestra como se ha realizado su ensamblaje. El primer paso fue crear un bloque con unión encolada, a la que más tarde se le dio una capa de lijado para eliminar la cola sobrante y mejorar el aspecto superficial. Posteriormente, se ubicó el motor con el casquillo.

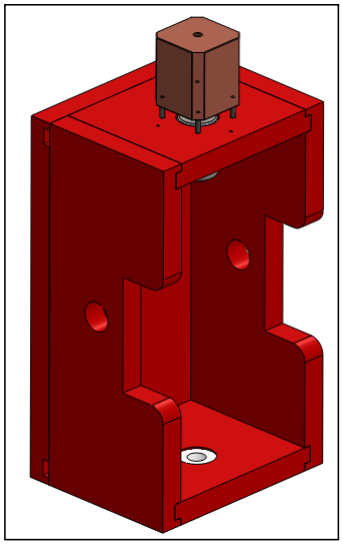
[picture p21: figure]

Ilustración 52. Bloque cabeza

El bloque interno también se encoló, pero esta vez se mecanizó en APM:

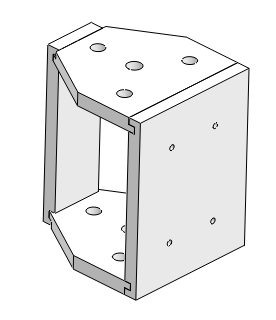
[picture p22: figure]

Ilustración 53. Bloque cabeza interno

Se insertaron los redondos de acero con los soportes. Es muy importante aclarar que la unión entre los redondos y el soporte es mediante presión. De esta forma, el molde superior se puede deslizar para no interferir con el casquillo una vez que se introduzca en el bloque principal.

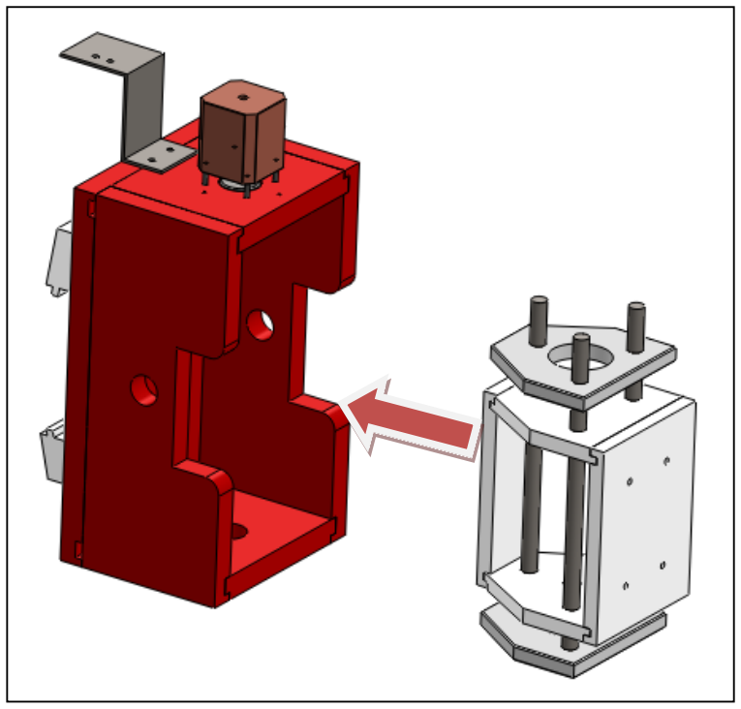
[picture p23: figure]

Ilustración 54. Inserción de la cabeza

Hecho esto, se atornillaron los dos soportes sobre el techo y el suelo del bloque cabeza. Finalmente, bastó con insertar desde abajo el tornillo roscado y el tope para contenerlo.

La lista de piezas es la siguiente:

Nombre de archivo | Cantidad | Masa
Tornillo M3 x 0.5 x 30 | 4 | 0,26
Apoyo tornillo sin fin baquelita | 1 | 15,34
Cabeza soporte ejes | 2 | 45,93
Cabeza separación interior | 1 | 51
Cabeza interior superior | 2 | 79,68
Cabeza soporte cadena porta cables | 1 | 84,08
Cabeza guía macho | 2 | 91,64
Cabeza interior delante | 1 | 126,99
Eje calibrado | 3 | 134,54
Cabeza superior | 1 | 136,47
Cabeza inferior | 1 | 137,91
Casquillo | 1 | 143,69
Tornillo 226 | 1 | 168,77
Cabeza lateral derecho | 1 | 250,95
Cabeza lateral izquierdo | 1 | 250,95
Cabeza atrás | 1 | 414,29
Motor Nema 23 | 1 | 721,39

El frente de la cabeza dispone de cuatro taladros. La idea es emplearlos para ubicar soportes específicos para las diferentes herramientas. Se ha dispuesto un hueco de 35x80mm para facilitar la tarea de atornillar el soporte. Esta generalidad permitirá el empleo de herramientas de dimensiones múltiples.

Ilustración 55. Hueco cabeza para atornillar soporte

El par máximo que puede ofrecer el motor influye directamente en el peso máximo de la herramienta que puede levantar el eje Z. Obtenerlo teóricamente complejo, por lo que se han realizado una serie de experimentos estocásticos posando diferentes pesos. Finalmente, el conjunto ha sido capaz de levantar hasta 3 kilogramos sin perder ningún paso.

Más adelante se detallan las herramientas que se han montado en la máquina durante la ejecución del proyecto, y se muestra la forma en la que se han construido los diferentes soportes, fabricados principalmente en acero. A continuación se muestra una imagen del CNC durante su desarrollo:

Ilustración 56. Estructura del CNC en desarrollo

### 3.3.6 Acabado final y pintura

Trabajar con madera requiere de un pequeño sobreesfuerzo con respecto al uso de perfilería de aluminio. No basta con cortar las piezas, si se quiere obtener un resultado perfecto, hay que realizar posteriormente un proceso de mejora del acabado superficial. En este caso el proceso ha consistido en suavizar las aristas con una fresadora, seguido de un lijado en dos etapas para preparar la madera para la capa de pintura.

Una vez que se ha realizado el ensamblaje y se ha verificado que todas las piezas encajan adecuadamente, se ha desmontado completamente la máquina. Pieza a pieza, se han suavizado las aristas con el uso de una fresadora. Esto proporciona un acabado más suave y además aumenta la durabilidad de la pintura, ya que la laca se suele desconchar con el paso del tiempo en las esquinas.

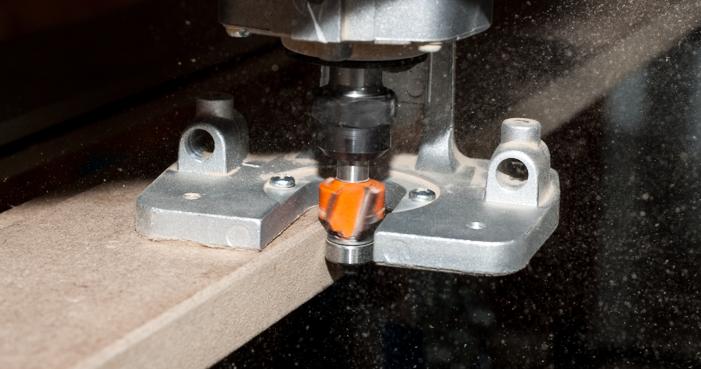
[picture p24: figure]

Ilustración 57. Suavizado de aristas

Tras esto, y de nuevo pieza a pieza, se ha lijado por completo con una lija de grano grueso y posteriormente se ha efectuado una segunda pasada con otra lija más suave, dejándolas listas para la fase de pintura.

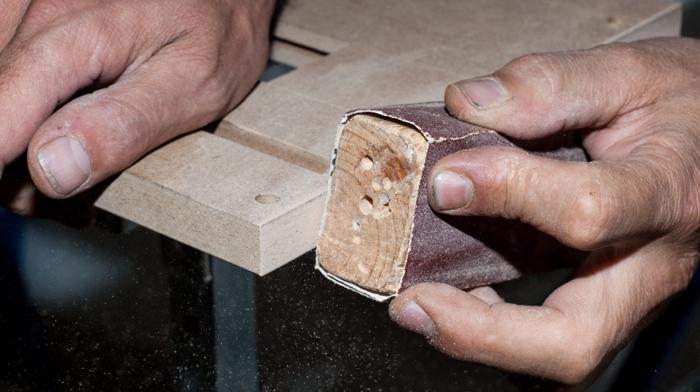
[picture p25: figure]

Ilustración 58. Lijado de desbaste

Ilustración 59. Lijado final

Todas las piezas se han llevado a un pintor profesional para aplicar la laca. El procedimiento consiste en aplicar en primer lugar una capa de imprimación de pintura de poliuretano. Tras el secado se lija la superficie y se vuelve a aplicar otra capa de pintura de poliuretano. El acabado final es perfecto.

El color elegido es blanco mate para la mayor parte de las piezas, y la cabeza junto a la guía de la cadena portacables superior en rojo mate, con el fin de transmitir sensación de peligro.

### 3.3.7 Ensamblaje final

Con todas las piezas listas, ya llega el momento de realizar el montaje final. Además de la cabeza, las únicas piezas que no se han ensamblado con tornillos son los dos laterales, con el fin de conseguir un bloque como soporte.

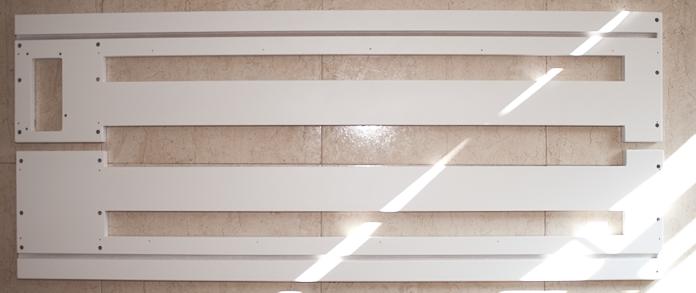
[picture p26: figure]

Ilustración 60. Laterales de la máquina ensamblados

Nótese el detalle de los taladros para los mechones de 8mm de haya con el fin de obtener un conjunto más robusto.

Ilustración 61. Mechones en los laterales

Tras efectuar el resto del ensamblaje, el resultado final es:

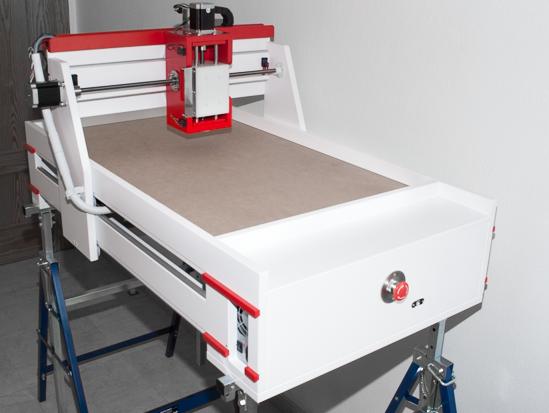
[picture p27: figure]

Ilustración 62. Ensamblaje final de la máquina

### 3.3.8 Cableado

Aún queda un aspecto crucial, y es encontrar la forma óptima de disponer todo el cable. Es muy importante porque la cantidad de cable es elevada: el uso de seis finales de carrera implica doce hilos de cable que no pueden restringir el movimiento de la cabeza a las posiciones más lejanas, así como los tres motores, que siendo cada uno a cuatro hilos se tienen otros doce cables. Se ha pretendido ocultar todo el cable en la medida de lo posible y se ha facilitado el desplazamiento de este mediante el uso cadena portacables en los ejes X e Y.

El cableado elegido no ha sido arbitrario. Se trata de uno con denominación “robótico”, perfectamente flexible y de plástico especialmente duradero frente a flexiones y desgaste por movimiento. La cantidad total de cable es:

Elemento | Longitud | Hilos | Total
Motor eje Y | 0.2 | 4 | 0.2
Motor eje X | 1.5 | 4 | 1.5
Motor eje Z | 2.5 | 4 | 2.5
F.C. Y+ | 1.1 | 2 | 1.1*2
F.C. Y- | 0.4 | 2 | 0.4*2
F.C. X+ | 2.4 | 2 | 2.4*2
F.C. X- | 2.1 | 2 | 2.1*2
F.C.Z+ | 2.5 | 2 | 2.5*2
F.C. Z- | 2.5 | 2 | 2.5*2
26.2

Unidades en metros. F.C. Final de Carrera. Los motores emplean manguera de cable a cuatro hilos, mientras que los finales de carrera dos hilos de cable de 1mm.

## 3.4 Herramientas

El análisis de las herramientas no se ha incluido el apartado de potencia ya que es preferible estudiarlo desde un punto de vista de fundamentos de fabricación, más que como un dispositivo electrónico. Al fin y al cabo las diferentes herramientas se han adquirido por empresas terceras y no tienen más complicación para hacerlas funcionar que conectarlas. Lo realmente delicado, es analizar cual es más adecuada para efectuar diferentes procesos.

Un dispositivo de control numérico es un aparato de propósito general. Las limitaciones se encuentran en la cantidad de ejes de interpolación y en la herramienta. La forma de obtener superficies, se puede efectuar mediante deposición de material (impresión 3D), o mediante eliminación de material. Un diferente software de control habría permitido emplearlo como dispositivo de impresión 3D, que para nada es el objetivo de este trabajo. Es por esto por lo que a continuación se muestran las diferentes herramientas empleadas, un análisis sobre ellas y las diferentes características de sus resultados, pero siempre bajo la misma premisa: se tratan de dispositivos de mecanizado mediante eliminación de material.

### 3.4.1 Fresadora Dremel 3000

Se trata de una pequeña fresadora de la marca Dremel. Sus pequeñas dimensiones y facilidad para situarla en un soporte la convirtieron en la primera candidata a ser controlada. Cuenta con una gran cantidad de accesorios y fresas de pequeño tamaño que ayudan a obtener resultados de precisión más que aceptable.

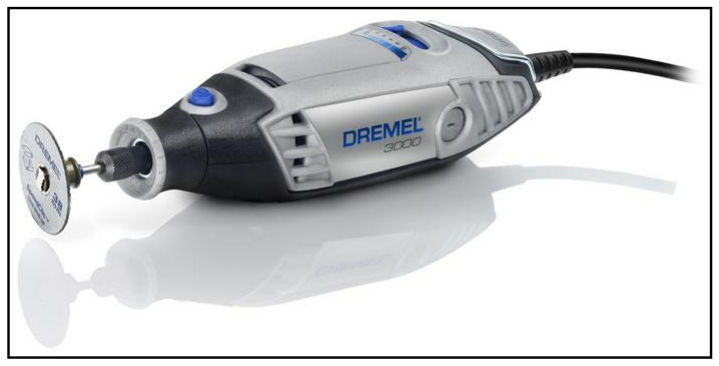
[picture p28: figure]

Ilustración 63. Dremel 3000

Sus principales características son:

Potencia | 130W
Tensión | 230V
Amperaje | 1.2A
Peso | 0.55Kg
Velocidad en vacío | 10000/33000rpm
Diámetro máximo vástago | 3.4mm

Pero lo que parecía una solución excelente, al final no ha hecho más que dar problemas. Aunque a nivel constructivo la herramienta cumple su función, y la potencia que proporciona es más que suficiente para realizar la mayoría de las tareas, su talón de Aquiles son los accesorios. Se han probado dos fresas, una esférica y otra cilíndrica (referencias 114 y 196 respectivamente). Cada una no ha aguantado más de dos horas de mecanizado con una velocidad de avance de tan solo 80mm/min, haciendo múltiples pasadas de profundidad 1.5mm. Debido a su geometría estas fresas no se pueden afilar, por lo que se han tenido que desechar.

Esta obsolescencia, no permite emplearla para largos procesos de mecanizado, pero sí que resulta idónea cuando se requiere de una gran precisión. Por ejemplo, se ha empleado para mecanizar espuma de poliuretano con una broca de diámetro 0.15mm.

Para situarla en la máquina, se ha elaborado el siguiente soporte en acero:

Ilustración 64. Soporte Dremel

Se puede observar una matriz de taladros para poder situarlo a diferentes alturas. Esto permite hacer diferentes reglajes en función de la pieza a trabajar. Para situar la fresadora, simplemente hay que enroscar el casquillo inferior que dispone la herramienta para los accesorios en el hueco inferior del soporte.

### 3.4.2 Fresadora Virutex FR192N

Fresadora profesional de marca Virutex de mayores dimensiones y potencia que la anterior. Incorpora un sistema de control electrónico, el cual mantiene la velocidad al margen del esfuerzo al que esté sometida la máquina.

Ilustración 65. Virutex FR192N

Sus principales características son:

Potencia | 750W
Tensión | 230V
Peso | 1.8Kg
Velocidad en vacío | 14000/30000rpm
Diámetro máximo vástago | 8mm

Se han efectuado una serie de modificaciones en la herramienta para adaptarla al soporte. En concreto se ha cortado un perno para acoplar accesorios y se han realizado cuatro agujeros roscados en la base:

Ilustración 66. Detalle taladros base fresadora

El elevado peso de la máquina no ha supuesto ningún problema y el motor del eje Z la mueve sin problema. Esta solución otorgará resultados de una gran calidad, contando en todo momento con accesorios profesionales de alta durabilidad y elevada relación ciclos de trabajo/precio.

Para poder ubicar esta fresadora de forma segura y robusta, se ha fabricado el siguiente accesorio:

Ilustración 67. Soporte Virutex

Debido al peso de la fresadora, se han soldado dos tirantes en ambos extremos, otorgando una gran solidez al conjunto. Para ubicar la máquina sobre el soporte, se han efectuado cuatro taladros roscados en la base de aluminio de la fresadora.

### 3.4.3 Láser 2W (445nm)

El mecanizado por láser ofrece tantas ventajas, que ha resultado irresistible de probarlo en esta máquina, aunque sea de forma experimental. Antes de explicar el láser empleado, se va a describir muy resumidamente en qué consiste esta tecnología y sus ventajas con respecto a métodos de fabricación convencionales.

Esta tecnología se basa en la generación de un rayo láser de alta potencia incidente sobre una pieza, consiguiendo una elevada densidad de potencia que produce la volatilización del material. El rayo láser erosiona el material en múltiples capas obteniendo la geometría y profundidad requerida.

Se trata de un procedimiento de fabricación no convencional mediante mecanizado de índole térmica. Es una tecnología costosa de reciente aplicación en la industria, pero debido a sus grandes virtudes, cada vez está siendo más utilizada. Una de las industrias que mayormente absorbe esta actividad es la industria del automóvil y la industria auxiliar del automóvil.

El proceso se basa en ubicar una alta densidad de potencia de un rayo láser enfocado sobre el material a procesar. El calor necesario para la vaporización es aproximadamente 10 veces superior al calor que hay que suministrar para conseguir la fusión de un material.

La generación del láser se basa en el fenómeno de la emisión inducida o estimulada para generar un haz de luz coherente. Las principales características del haz láser son:

■ | Monocromía: solo posee una longitud de onda. Los láseres con mayor
| rendimiento son los que emiten en el rango de infrarrojo y en el rango de
| ultravioleta.
■ | Coherencia: todas las ondas se encuentran en fase.
■ | Dirección: conservación de la energía a lo largo de la trayectoria.

Es necesario acompañar este tipo de mecanizado con un flujo de gas que elimina el material fundido y protege las lentes focalizadoras.

Normalmente este gas suele ser aire, para materiales no metálicos, ya que no existe peligro de oxidación. Para materiales metálicos se suelen emplear gases inertes como por ejemplo el argón.

Las principales ventajas del láser son:

■ | No se produce desgaste, rotura ni colisión de la herramienta.
■ | Es posible mecanizar casi todo tipo de materiales, desde aceros, aleaciones
| termoresistentes, cerámicas, silicio, etcétera.
■ | No se produce viruta.
■ | Se pueden obtener formas complejas.
■ | No se precisa de cambio de herramienta.
■ | Proceso limpio y rápido.
■ | Mejor aprovechamiento del material debido a que la anchura del surco
| generado es mínima.
■ | La pieza producida no precisa ningún tratamiento posterior ni limpieza.
■ | No se generan residuos tóxicos o agresivos.

Puesto que no todo pueden ser ventajas, a continuación se citan los mayores problemas que surgen en el empleo del láser:

■ | Coste elevado de la instalación.
■ | Algunos materiales tales como oro, plata, o cobre, son difícilmente
| mecanizables por láser debido a la alta reflectividad y conductividad térmica
| que presentan.
■ | Generalmente no se usa para espesores de más de 20 mm, ya que a partir de
| allí es muy difícil enfocar el láser.
■ | Hay que tener grandes precauciones. Existen dos factores principales de
| riesgo:
| • Electricidad.
| • Exposición a la luz láser (ESPECIALMENTE PELIGROSOS LOS RAYOS LÁSER NO VISIBLES POR EL OJO HUMANO).

Hecho este repaso general sobre la tecnología láser, su aplicación en este proyecto no ha sido, dicho de alguna forma, excesivamente profesional. Pero sí enriquecedor y apasionante. El simple hecho de pensar que se está mecanizando con luz, es apasionante.

Para llevarlo a cabo, la Universidad Politécnica de Cartagena ha adquirido un láser en la web lasers-pointers.com. En concreto el modelo de 2000mW con una longitud de onda de 445nm.

Ilustración 68. Láser 2W (445nm)

Es fundamental de cierta protección cuando se está trabajando con este tipo de herramientas. Por tanto, es crucial disponer de gafas de protección cuando se esté trabajando con el dispositivo, suministradas en la web donde se compró el dispositivo.

El soporte que se ha diseñado para el láser tiene el siguiente aspecto:

Ilustración 69. Soporte láser en SolidWorks

La gran genialidad del uso del láser en esta máquina es que se puede enfocar a la mínima distancia de enfoque, por lo que se aprovecha toda la potencia del láser.

Con respecto a su activación, lo óptimo es generar el fichero de control numérico con un postprocesador específico para láser o corte por plasma, de esta forma se apaga el haz de luz cuando se realizan movimientos en G0. El problema es que el láser dispone de un botón de encendido físico, por lo que en este proyecto al efectuar movimientos rápidos se apaga manualmente el láser, dejando como trabajo futuro el dotar al dispositivo de un accionamiento mecánico para poder apagarlo y encenderlo automáticamente.

Aplicación práctica

La potencia del láser limita los materiales que se pueden mecanizar. No obstante, ha sido más que suficiente para realizar cortes en materiales como papel, cartón, poliuretano y poliestireno, con una precisión asombrosa y sin necesidad de compensar ningún radio de herramienta, pues el haz, cuando está correctamente adecuado, tiene un tamaño infinitesimal.

También realiza pirograbados en materiales como madera o cuero.

Una fuerte limitación es que se calienta. Mucho. No es recomendable tenerlo más de veinte segundos encendido sin parar con el enfoque situado muy cerca del foco emisor. Además el consumo de batería es bastante elevado. Como resultado, no permite mecanizar piezas de geometría excesivamente compleja. En un futuro se podría diseñar un disipador cilíndrico como los que se ponen en los motores de continua para ayudar a eliminar calor.

A modo de aplicación, a continuación se muestra un ejemplo de grabado. Cabe destacar que con el fin de mejorar la calidad de la imagen se han realizado tres pasadas para obtener un trazo más grueso. El fichero de control numérico se ha obtenido mediante el empleo de Inkscape con el plugin Gcodetools (software gratuito y libre).

Ilustración 70. Ejemplo de aplicación de grabado mediante láser

## 3.5 Interfase máquina - ordenador

El programa empleado es GRBL Controller, totalmente compatible con GRBL. Se trata de un software diseñado para enviar código G a dispositivos de control numérico de 3 ejes. Aunque no es el más inteligente, dispone de herramientas más que suficientes para enviar a la máquina cualquier programa G previamente creado con post-procesadores TinyG por ejemplo.

Este software está escrito usando las librerías multiplataforma de Qt, así como la librería QextSerialPort para simplificar el proceso para elegir el puerto serie USB correcto. Este desarrollo multiplataforma le permite trabajar sobre Windows, Mac y Linux.

Este programa ha recibido multitud de actualizaciones en el último año, y continúa recibiendo. La última, fue lanzada tan solo un mes antes de comenzar a redactar el proyecto. A continuación se muestra una tabla con la compatibilidad de cada versión con las diferentes plataformas.

Versión | Compatibilidad
Windows | Mac | Linux
3.0 | SI | SI | SI
3.2 | SI | SI | X
3.3 | SI | SI | X
3.3.1 | SI | X | X
3.3.2 | SI | SI | X
3.3.3 | SI | X | X
3.3.4 | SI | X | X
3.3.5 | SI | X | X
3.3.9 | SI | X | X
3.4 | SI | X | X
3.4.2 | SI | X | X
3.4.4 | SI | SI | X
3.4.5 | SI | X | X
3.4.6 | SI | SI | X
3.5 | SI | SI | X
3.5.1 | SI | X | X
3.6.1 | SI | X | X

Una vez que se ejecuta el programa, aparece una ventana sobre la que apenas se puede interactuar. Si el controlador está correctamente conectado, con el puerto serial correctamente asignado y con el sketch de GRBL introducido, al pinchar sobre “Open”, el programa accede a la programación del controlador, la carga, y la muestra en la ventana:

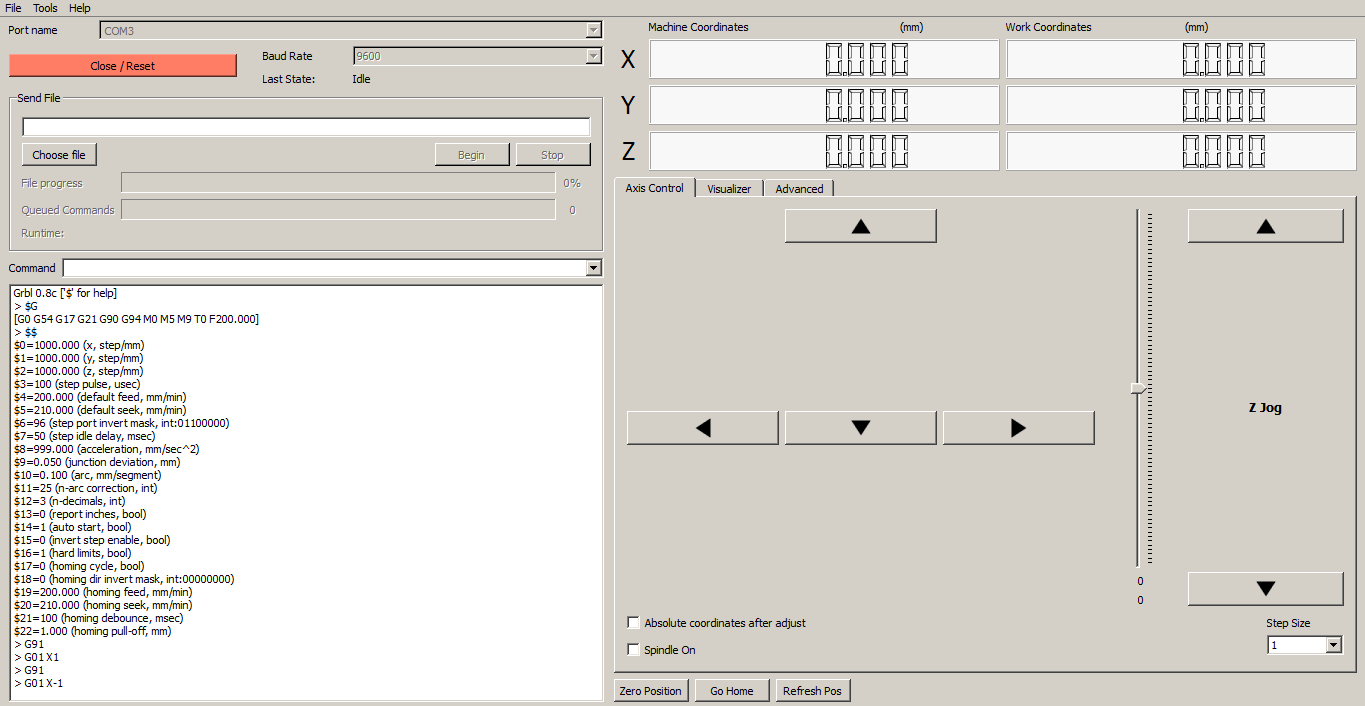
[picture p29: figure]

En esta ventana se pueden apreciar cinco partes totalmente diferenciadas:

■ Barra de herramientas: más adelante se explicarán todas las opciones de que dispone GRBL.
■ Inicialización de GRBL: tras seleccionar la velocidad de comunicación en baudios, el puerto serial y conectar Arduino, al pulsar abrir el programa inicializa.
■ Ventana de comandos y explorador de ficheros G: desde esta ventana se pueden enviar comandos a GRBL, así como cargar un programa de control numérico. También se muestran los comandos que se han ejecutado y en el caso de haberlas, las salidas que proporcionan esos comandos.
■ Coordenadas de la máquina y de trabajo.
■ Control manual. Visualizador. Acceso a configuración.

Desde la pestaña “herramientas” de la barra de herramientas, se tiene acceso a cuatro opciones de configuración. La primera ventana es la de opciones generales y tiene este aspecto:

Si la primera opción no está seleccionada, las coordenadas que se van a mostrar en la ventana principal, estarán en pulgadas. Si está seleccionada, se mostrarán en milímetros.

Si la carga agresiva de GRBL no está activada, GRBL va a esperar una respuesta del fichero después de ejecutar cada comando. Si está activada, el fichero va a enviar comandos hasta llenar el buffer de GRBL, y se va a encargar de que el buffer esté en todo momento lleno. Esto permite una mayor velocidad en la ejecución de las instrucciones, pero tiene un problema. Si se pulsa el botón de parada (dentro de GRBL Controller, no la seta de emergencia), la parada no es inmediata. Primero se deben de ejecutar todas las instrucciones que hay en el buffer hasta llegar a la orden de paro. La mejor solución para pararlo es simplemente pulsando la seta de emergencia en caso de que surjan problemas, y dejar de este modo la carga agresiva activada.

La siguiente opción, escribe un fichero de depuración llamado GrblController.log en la carpeta por defecto del computador con todos los mensajes de diagnóstico y estado. Este archivo se borra siempre GRBL Controller se reinicia. Permite depurar problemas si ocurre algo extraño, e incluso se puede enviar a la web del autor para que analice lo que ha ocurrido y solucionar fallos en un futuro.

La siguiente opción “segundos de espera hasta respuesta” se encarga de abortar un trabajo con un fichero si GRBL no responde tras el tiempo configurado. Es conveniente que este tiempo sea relativamente grande en el caso de realizar trayectorias largas.

Por último, “Z-Jog Rate” es la velocidad a la que se va a mover el eje Z cuando se acciona mediante el slider de la ventana principal llamado Z Jog.

La siguiente pestaña, llamada filtro, es la siguiente:

Un valor muy importante es la longitud del buffer que va a almacenar cada línea de código
G. Si la línea de código G contiene demasiados números decimales y el buffer se llena, entonces la máquina se va a comportar de una forma indeseable. Por ejemplo, es probable que esta línea genere problemas:

G01 x2.35484876666594 y1.0021848787554 z5.54545775454521

Es habitual que programas de CAM generen este tipo de ficheros de control numérico por defecto. Otorgan una sensación falsa de precisión pues jamás la máquina va a ser capaz de efectuar movimientos discretos de millonésimas de milímetro. Lo único que va a hacer es llenar el buffer de GRBL y provocar problemas. Lo adecuado es aumentar el buffer de GRBL en su máximo valor (70), y restringir el programa de CAM a no generar más de cuatro cifras después del decimal.

La tercera pestaña, tiene que ver con los ejes:

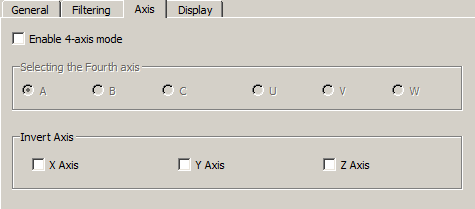
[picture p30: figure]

En este proyecto no se ha empleado el cuarto eje, por lo que realmente no se dispone de demasiada información a cerca de la configuración de este eje. No obstante, como ya se ha dicho, GRBL no dispone de soporte para interpolar en más de tres ejes.

La opción de invertir ejes, además de invertir el funcionamiento del pin DIR de los drivers, invierte el sentido cuando se lee un fichero G. Si por ejemplo al presionar el botón Y+ en modo manual la máquina avanza hacia Y-, se recomienda no invertir desde esta ventana la dirección del eje Y, y hacerlo desde una máscara diseñada específicamente para esto y que se explicará en el apartado 6.3.

La última pestaña es la de visualización:

Simplemente permite que GRBL envíe información a cerca de donde se encuentra la máquina (donde cree él que está) y se muestre en los displays de la ventana principal. Cuanto menor sea el tiempo de refresco, más carga va a tener GRBL y más lento va a ir la ejecución del programa.

Con el fin de optimizar este proceso, en la última versión de GRBL Controller se ha habilitado una tercera opción que hace que no se actualice la posición al realizar un movimiento manual (se muestra activa en la captura de pantalla anterior). Esto reduce enormemente la carga de GRBL.

Existen algunos botones en el programa que al pulsarlos realizan acciones que también se pueden realizar mediante comandos. Esto simplifica y permite un flujo de trabajo más cómodo con la máquina.
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

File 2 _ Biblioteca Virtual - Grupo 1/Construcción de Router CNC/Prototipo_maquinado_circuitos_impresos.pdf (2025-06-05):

## PROTOTIPO DE MAQUINADO PARA FABRICACION´ DE CIRCUITOS IMPRESOS CON FRESADORA

Hector Hern ´ | an Rangel Cubides and Luis Carlos Sevilla Heredia ´

Resumen—Este trabajo presenta el diseno de una ˜
maquina de control num ´ | erico computarizado (CNC) para ´
el fresado de circuitos impresos o PCB (Printed Circuit Board) . El sistema se basa en el control del posicionamiento de un motor de corriente alterna (AC), el cual se encarga del fresado y taladrado de la baquelita, por medio de una estructura de tres ejes ortogonales accionados con motores paso. Se desarrollo un software que permite leer archivos Gerber¹
, creados por un programa de diseno para PCB, ˜ este realiza un esquema preliminar del diseno del PCB y ˜ env´ıa las coordenadas a traves del puerto USB, a la tarjeta ´ de control de los motores.
I. INTRODUCCION´
Cada d´ıa se hace necesario que la presentacion de ´ los circuitos impresos, tanto para la educacion como ´ para la comercializacion, est ´ en a la vanguardia de ´ las grandes industrias nacionales e internacionales, teniendo en cuenta que sean funcionales y acordes
a los parametros del dise ´ | no. Adem ˜ | as en la gran ´
mayor´ıa de los casos se busca la produccion en ´ masa de manera economica, eficiente, segura y ´
rapida, y es por esto que se piensa en la fabricaci ´ | on´
de un prototipo de maquina para la fabricaci ´ | on de ´
circuitos impresos de una sola capa de cobre en baquelita por fresado, sin antisolder²
, ni mascara
de componentes, empleando un sistema de control
numerico, con una interfaz gr ´ | afica que permita ´
importar el diseno del circuito desde un programa ˜ CAD (Computer-Aided Design), que mejore los procesos de produccion en el entorno. ´

El control numerico computarizado [1], actualmente ´

H. Rangel Estudiante de Ingenier´ıa Electronica, Universidad ´
Pedagogica y Tecnol ´ | ogica de Colombia, Sede Seccional Sogamoso, ´
Grupo de investigacion GIRA ´ | herahecu@gmail.com
C. Sevilla Estudiante de Ingenier´ıa Electronica, Universidad ´
Pedagogica y Tecnol ´ | ogica de Colombia, Sede Seccional Sogamoso, ´
Grupo de investigacion GIRA ´ | solrac00@gmail.com
1Archivos ASCII con coordenadas e instrucciones simples 2Mezcla especial con propiedades dielectricas ´

se encuentra en desarrollo, brindando un nuevo campo de investigacion, con el cual es posible ´ enfocar futuros trabajos para diferentes aplicaciones en la industria colombiana. El primer desarrollo
en el area del CNC lo realiz ´ | o el inventor ´
norteamericano John T. Parsons junto con su empleado Frank L. Stulen, en la decada de 1940 ´
[2]; la primera maquina de fresar se construy ´ | o en ´
1818 y fue disenada por el estadounidense Eli ˜ Whitney, con el fin de agilizar la construccion´ de fusiles en el estado de Connecticut [3], y desde ah´ı en adelante todos los esfuerzos se han encaminado a incrementar la productividad,
precision, rapidez y flexibilidad de las m ´ | aquinas- ´
herramienta. Su uso ha permitido la mecanizacion´ de piezas muy complejas, especialmente en la
industria aeronautica, que dif ´ | ´ıcilmente se hubieran
podido fabricar de forma manual. De igual manera se han empleado sistemas controlados por computadora para el diseno de piezas dentales en ˜ ceramica como lo es el CEREC de la marca Sirona ´ de Alemania [4]. En el desarrollo de este tipo de herramientas se emplean diferentes sistemas roboticos, como el implementado en el laboratorio ´ de manufactura del Instituto Tecnologico de Puebla ´ [5]. Actualmente en Colombia se encuentra el CNC en surgimiento, teniendo algunos diplomados en universidades como la EAFIT y en desarrollo algunas investigaciones y proyectos. Sin embargo
es un area de poca avance en investigaci ´ | on y es ´
por esto que se pretende realizar un prototipo de
una maquina basada en esta tecnolog ´ | ´ıa que permita
suplir algunas necesidades emergentes cuando son fabricados circuitos impresos que requieren de cierta precision. ´
En el area de la electr ´ | onica es indispensable ´
el ahorro de tiempo para mayor eficiencia en el trabajo que se requiere para la fabricacion´

de PCBs. Este procedimiento es dispendioso ya que se precisa la utilizacion de ´ acido, marcadores ´ especiales o impresora laser y papel; esto en el caso
de la tecnica denominada papel transfer. Adem ´ | as de ´
una disponibilidad total de la persona que realiza el procedimiento, debido a que este es meramente manual. El tiempo de fabricacion es incierto ´ dependiendo de la experiencia del fabricante, del cuidado al realizarlo, de los materiales y es algo peligroso debido a estos. Este es el metodo ´
mas econ ´ | omico para la fabricaci ´ | on de PCBs, sin ´
embargo, cuando es necesario un error cercano a cero y ademas producir una serie de circuitos ´ iguales el objetivo se complica, convirtiendose en ´ un verdadero problema, teniendo que realizar el mismo procedimiento para cada circuito.

II. DESCRIPCION´
El sistema sera descrito en base a los siguientes ´ componentes:
- Software: Incluye el diseno del PCB, la gen- ˜
| eracion y lectura de archivos descriptivos, ´
interfaz de usuario, visualizacion y comuni- ´
cacion de las coordenadas y dem ´ | as datos nece- ´
| sarios al controlador a traves del puerto USB ´ del computador.
- Hardware: Constituida por los dispositivos
| electronicos, se encarga de recibir los datos ´
del computador, y generar las senales de con- ˜ trol tanto para cada uno de los ejes de posicionamiento, como para el motor de fresado.
- Dispositivo mecanico: Corresponde a la es- ´
| tructura mecanica, la cual consta de tres ejes ´
de posicionamiento, con sus correspondientes
| actuadores y sensores; ademas de un motor AC ´ para el fresado.

II-A. Software
II-A1. Diseno del PCB y generaci ˜ | on de ´
archivos Gerber: El diseno de un circuito impreso ˜ a menudo requiere de programas de diseno˜ electronico automatizado EDA(Electronic Design ´ Automation), para distribuir e interconectar los componentes. Estos programas convierten el esquematico en una lista de los pines y nodos ´ (netlist) del circuito, a los que se conectan los pines de los componentes. La lista de nodos sera cargada posteriormente en un programa de ´ ruteo generando el esquema del PCB, y por ultimo ´ se crea un conjunto de datos e instrucciones descriptivas almacenadas en un archivo en formato HPGL(Hewlett and Packard Graphics Language) o Gerber.

Para esta aplicacion se emplea el programa ´ de diseno Eagle 4.16r2 ˜

3
, que permite generar un
esquema de contornos de las l´ıneas del circuito impreso. Empleando este esquema es posible minimizar el desgaste de la herramienta de corte al realizar el fresado, ya que no sera necesario retirar ´ todo el metal hasta obtener las l´ıneas conductoras (figura 1a), sino unicamente los contornos de ´ dichas l´ıneas (figura 1b). Adicionalmente es posible generar un archivo en formato Gerber RS-274X, que contiene las coordenadas tanto de los contornos como de las perforaciones (pads).

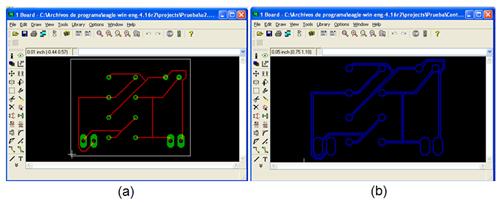
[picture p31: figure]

Figura 1. Esquema del circuito impreso (a) y de los contornos (b) en Eagle 4.16r2

II-A2. Interfaz de usuario y lectura de archivos
Gerber: Se desarrollo una aplicaci ´ | on en Visual ´
Basic 6.0 que permite abrir los archivos Gerber, realizar la lectura de las instrucciones, e interpretar cada una de las caracter´ısticas del PCB descritas, entre ellas el tipo de interpolacion, el formato ´ de las coordenadas, la unidad de medida (mm o pulgadas); y el tipo de movimiento, es decir desplazar sin trazar, desplazar trazando y marcar un punto (perforar). Con esta informacion el programa ´ realiza un esquema preliminar del PCB en pantalla (figura 2), es necesario cargar dos archivos uno para el trazado de las l´ıneas del circuito y el otro para la perforacion de los agujeros en los cuales se ´ ubican los dispositivos (figura 3).

3Version libre del software de CadSoft ´

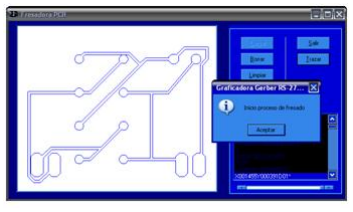
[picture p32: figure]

Figura 2. Vista preliminar del PCB

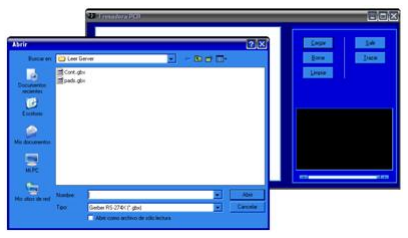
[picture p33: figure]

Figura 3. Apertura de archivos de contornos y pads

El proceso de fresado se inicia con un comando
dentro de la aplicacion, este genera la condici ´ | on de ´
cero es decir ubica la fresa en la coordenada (0, 0, 0). Una vez se ha ubicado en este punto se enciende el motor AC encargado del fresado. A continuacion´ el programa env´ıa las coordenadas de cada uno de los ejes al circuito de control y verifica la ejecucion´ de los movimientos, empleando el puerto USB.

II-B. Hardware
II-B1. El | Controlador: | El | controlador
esta inmerso en un microcontrolador PIC18F2550 ´ encargado de recibir las coordenadas para cada uno de los ejes provenientes del software del computador mediante el puerto USB, para luego enviarlas a cada uno de los microcontroladores PIC18F452 los cuales generan las respectivas secuencias para el movimiento de los motores paso y toman los datos de los sensores de movimiento de los ejes, mediante comunicacion I2C ´
| | | 4 (Inter
Integrated Circuit) [6] a 250 KHz, como se muestra

4Bus disenado por Phillips Semiconductors ˜

en la figura 4

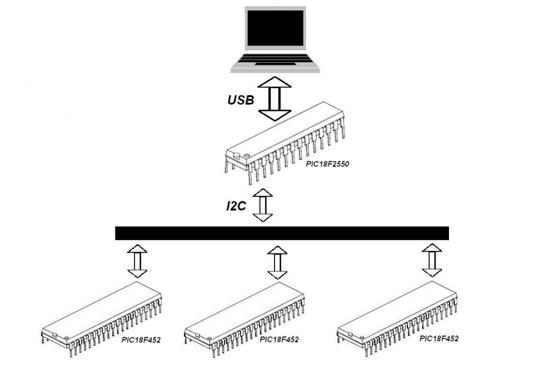
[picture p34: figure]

Figura 4. Esquema de comunicacion del prototipo ´

Comunicacion USB: Debido a la tendencia a ´ desaparecer de los puertos de entrada/salida del computador tales como el puerto paralelo y el puerto serial se opto por escoger para la interaccion del prototipo con el software ´ el puerto USB, el cual puede trabajar en dos diferentes modos uno a 1.5 Mbps⁵ (baja velocidad) o el otro a 12 Mbps (alta velocidad) utilizando este ultimo para el ´
desarrollo de la aplicacion. Tambi ´ | en fue ´
necesaria la creacion de los drivers de ´ instalacion los cuales se desarrollaron en el ´ software Microsoft Windows Server 2003 SP1 Driver Development Kit (DDK) con ayuda del ejemplo toaster del mismo.

Comunicacion I2C: Se configuraron de ´ manera adecuada los modulos incluidos ´ en los microcontroladores PIC 18F2550 y PIC18F452 de comunicacion MSSP (Master ´ Synchronous Serial Port), de tal manera que el PIC 18F2550 es el maestro y tres esclavos PIC18F452 a una frecuencia de 250 KHz; el maestro env´ıa cuatro datos provenientes del computador a cada uno de los esclavos proporcionandoles las coordenadas a las ´ cuales deben llegar cada uno de los ejes.

Programacion de los microcontroladores: El ´ firmware del microcontrolador 18F2550 se

5Mega bits por segundo desarrollo en lenguaje C con el compilador ´ PCWH, ya que este contiene las librer´ıas necesarias para la comunicacion USB, y ´ para los microcontroladores 18F452 se desarrollo en lenguaje ensamblador con el ´ software MPLAB de Microchip con el cual se tiene un control total del programa siendo la programacion totalmente transparente para ´ el programador.

II-B2. Etapa de Potencia:
Motores Paso: Con el fin de no tener ningun tipo de inconveniente de reinicio de ´ los microcontroladores se utilizaron opto acopladores 4N33 conectados a cada una de las salidas de los mismos. Para la conexion de ´
los motores paso se utilizo una configuraci ´ | on´
Darlington entre los opto acopladores y transistores BJT-NPN TIP 41C, para proteger los transistores del contra voltaje inductivo producido por los motores se conectaron diodos FR 206 como aparece en la figura 5

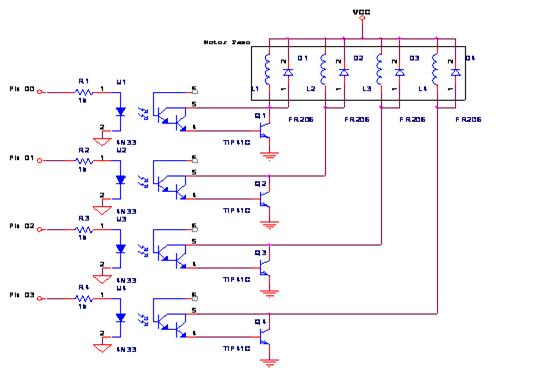
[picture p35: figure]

Figura 5. Esquema de conexion de los motores con la etapa de ´ potencia

Motor de corriente alterna: Esta comandado desde el software del computador a traves del ´ PIC 18F2550 conectado a este por el circuito mostrado en la figura 6 formado por un opto triac MOC 3021 y un triac BT 136-500. II-B3. Conjunto de Sensores: Se ubicaron sensores fines de curso para evitar que las piezas del prototipo sufran algun tipo de choque entre ellas, ´

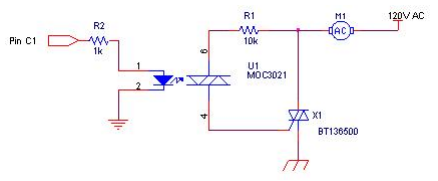
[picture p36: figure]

Figura 6. Esquema de conexion del motor de corriente alterna ´
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

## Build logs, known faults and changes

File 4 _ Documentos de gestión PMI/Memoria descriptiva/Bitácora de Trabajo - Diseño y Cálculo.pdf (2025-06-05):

# Bitácora de Trabajo:

# Equipo Diseño y Cálculo

Grupo 1.

# - Docentes:

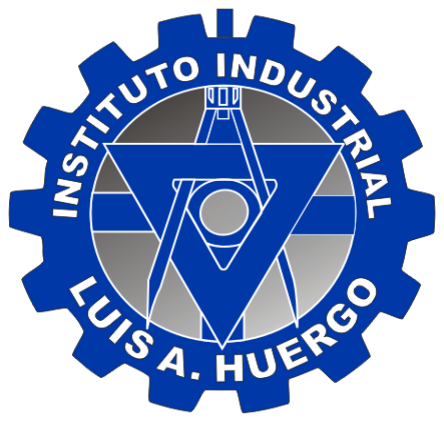
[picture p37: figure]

# - Osvaldo P. Ivani - Sebastián Amago Prato - Martín A. Ricciardelli - Juan Martín Hermida

# - Estudiantes: - Dante G. Mele Ientile (Project Manager) - León A. Martin - Hernán A. Silva - Nicolás L. Fertonani - Laureano M. Rivera Pascua

# - Curso: 4

# to Año Ciclo Superior - Electromecánica

Prácticas Profesionalizantes | Bitácora de Trabajo - Equipo Diseño y Cálculo

# - Blog de ajuste de Mecanizado: https://ingemecanica.com/tutorialsemanal/tutorialn19 .html (https://ingemecanica.com/tutorialsemanal/tutorialn19.html) Imanes-Monarca electrónica-3x8

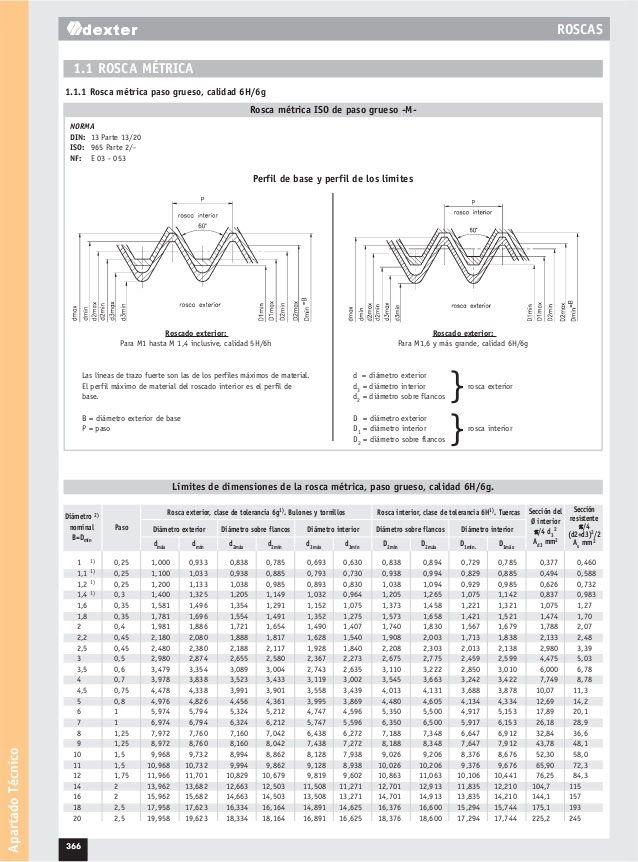
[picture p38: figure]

IILAH - Alumnos - Grupo 1: Fertonani, Martin, Mele Ientile, Rivera Pascua, Silva Página 1 de 25

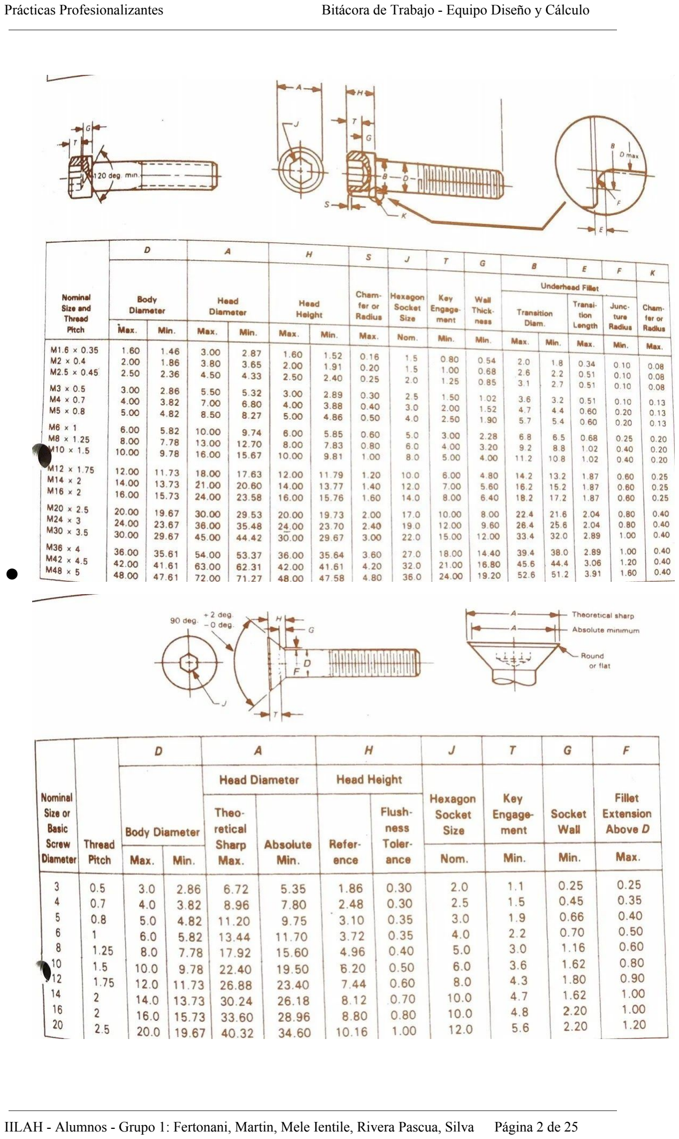
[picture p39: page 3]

●

IILAH - Alumnos - Grupo 1: Fertonani, Martin, Mele Ientile, Rivera Pascua, Silva Página 2 de 25

# - Chaponete: Ver ambos tornillos

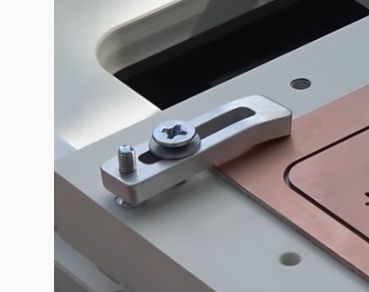
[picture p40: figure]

# https://wegstr.com/Aluminum-clamps-4-pcs

IILAH - Alumnos - Grupo 1: Fertonani, Martin, Mele Ientile, Rivera Pascua, Silva Página 3 de 25

# Retenes DBH

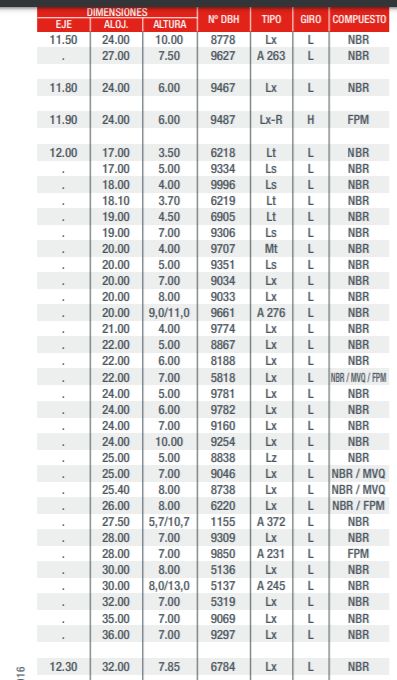
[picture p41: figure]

IILAH - Alumnos - Grupo 1: Fertonani, Martin, Mele Ientile, Rivera Pascua, Silva Página 4 de 25

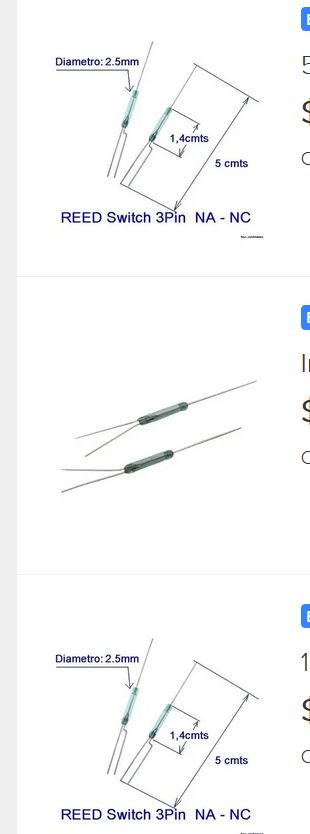
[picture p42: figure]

●

IILAH - Alumnos - Grupo 1: Fertonani, Martin, Mele Ientile, Rivera Pascua, Silva Página 5 de 25

# TUERCAS HEXAGONALES

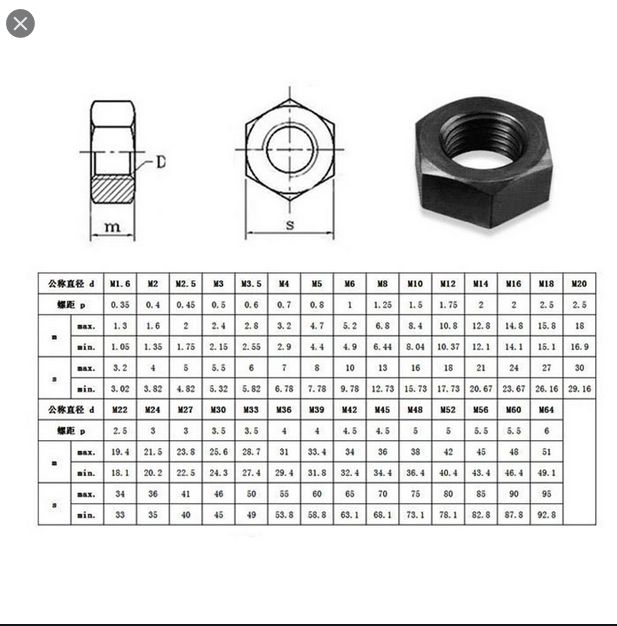
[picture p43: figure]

# - RECORDAR QUE SE VAN A HACER 2 CHAPONETES Y QUE LOS TORNILLOS CABEZA

FRESADA | PARA | ELLOS | VAN | A TENER

# DISTINTOS LARGOS (PUES, DEPENDE DEL OPERARIO, SU COMODIDAD, LA PLACA QUE QUIERA MECANIZAR, ETC.)

IILAH - Alumnos - Grupo 1: Fertonani, Martin, Mele Ientile, Rivera Pascua, Silva Página 6 de 25

# Volumen sólido 830390,000 mm³ 1725884,660 mm³ (laterales) Laureano Rivera Pascua

18:37

# 1017257,435 mm³ (frente) 1727353,563 mm³ (lateral izquierdo)

# pÁGINAS CON COSAS DE DIBUJO TÉCNICO:

# - http://dibujo.ramondelaguila.com/?page_id=926 - https://www.dibujotecnico.com/cortes-secciones-y-rotura s/ (https://www.dibujotecnico.com/cortes-secciones-y-roturas/)

# COMO CAMBIAR EL NOMBRE DE UNA PIEZA EN INVENTOR:

## https://knowledge.autodesk.com/es/support/inventor/troubleshooting/caas/sf dcarticles/sfdcarticles/ESP/Inventor-Renaming-file-names-of-Sub-Assem

blies-or-Parts.html (https://knowledge.autodesk.com/es/support/inventor/troubleshooting/caas/sfdcarticles/sfdcarticles/ESP/Inventor-Renaming-file-names-of-Sub-Assemblies-or-Parts.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)

IILAH - Alumnos - Grupo 1: Fertonani, Martin, Mele Ientile, Rivera Pascua, Silva Página 7 de 25

## Arandelas

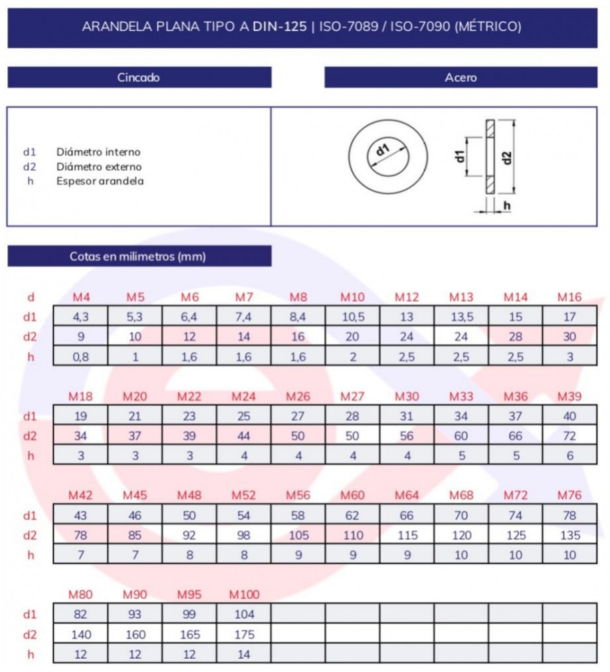
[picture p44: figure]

IILAH - Alumnos - Grupo 1: Fertonani, Martin, Mele Ientile, Rivera Pascua, Silva Página 8 de 25

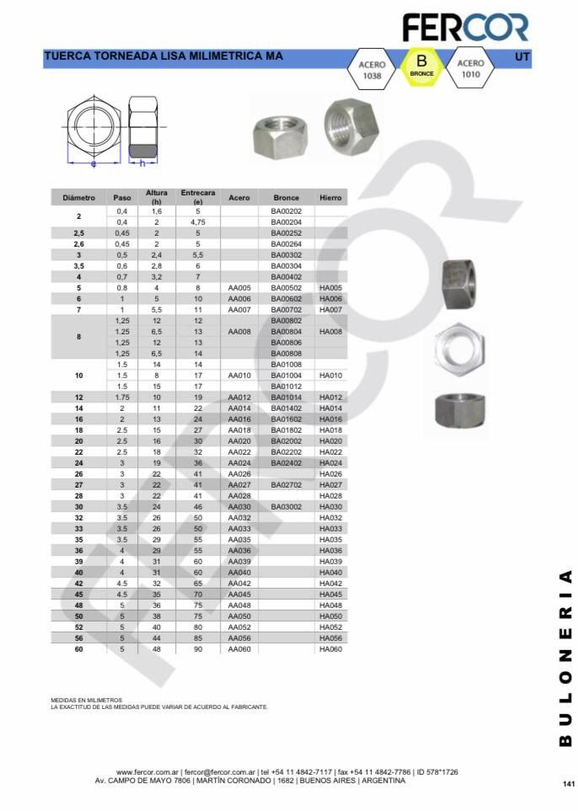
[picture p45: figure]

## Catalogo de tuercas remachables - Pag:https://meet.google.com/linkredirect?authuser=0&dest=http%3A%2F %2Fwww.selflex.com.ar%2Fargenrap-acerobajocarbono.html

IILAH - Alumnos - Grupo 1: Fertonani, Martin, Mele Ientile, Rivera Pascua, Silva Página 9 de 25

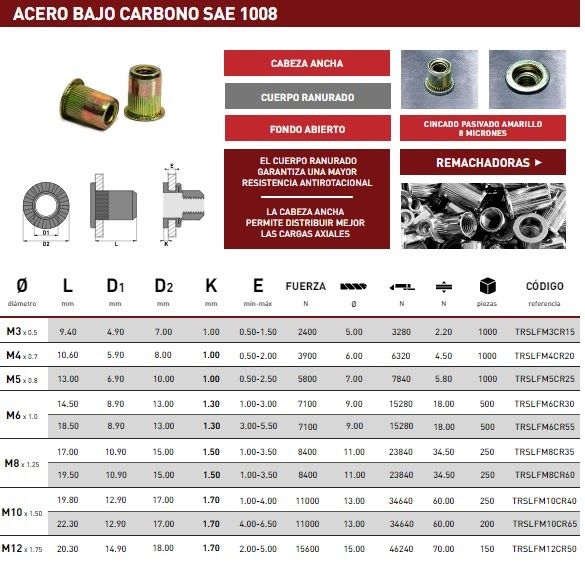
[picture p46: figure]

# ETAPA 4:

IILAH - Alumnos - Grupo 1: Fertonani, Martin, Mele Ientile, Rivera Pascua, Silva Página 10 de 25

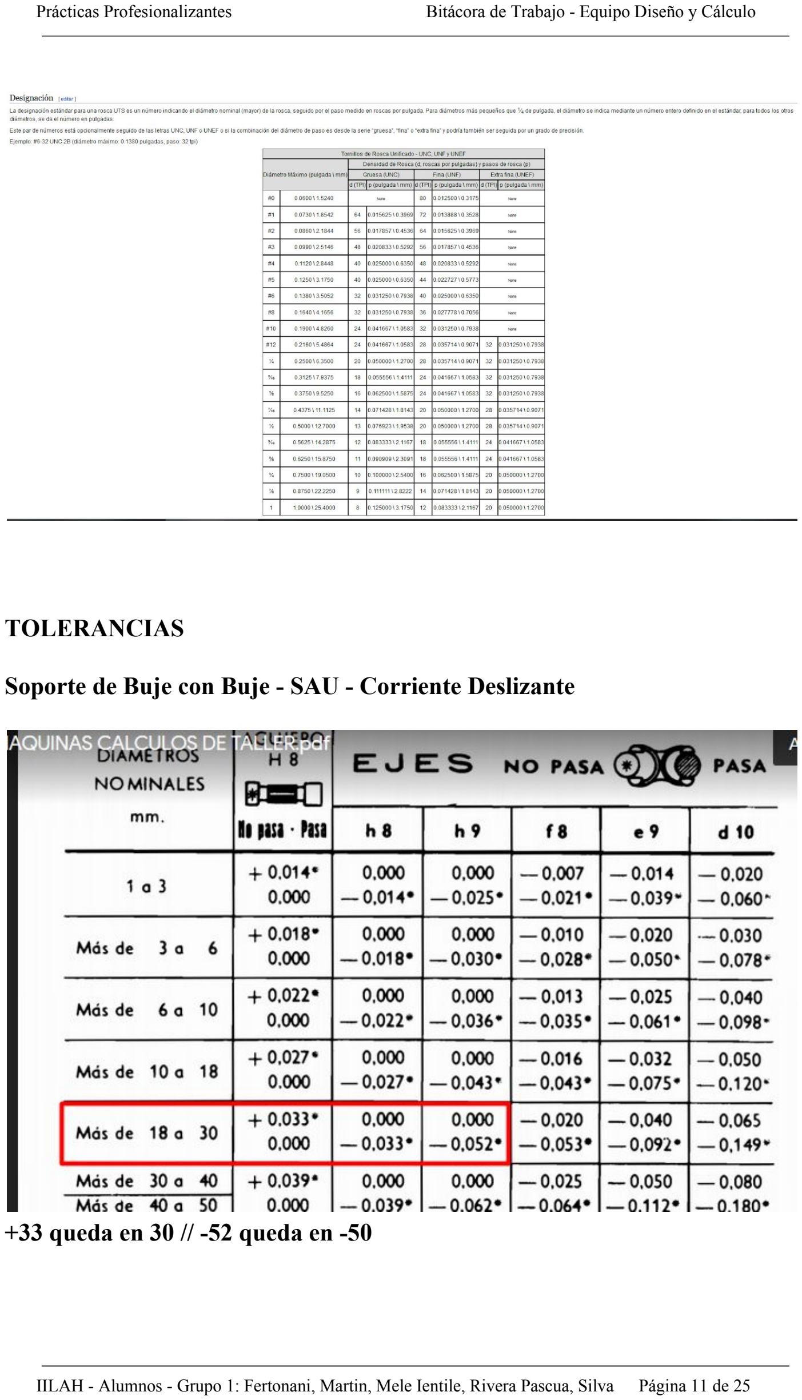
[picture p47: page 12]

## TOLERANCIAS

## Soporte de Buje con Buje - SAU - Corriente Deslizante

## +33 queda en 30 // -52 queda en -50

IILAH - Alumnos - Grupo 1: Fertonani, Martin, Mele Ientile, Rivera Pascua, Silva Página 11 de 25

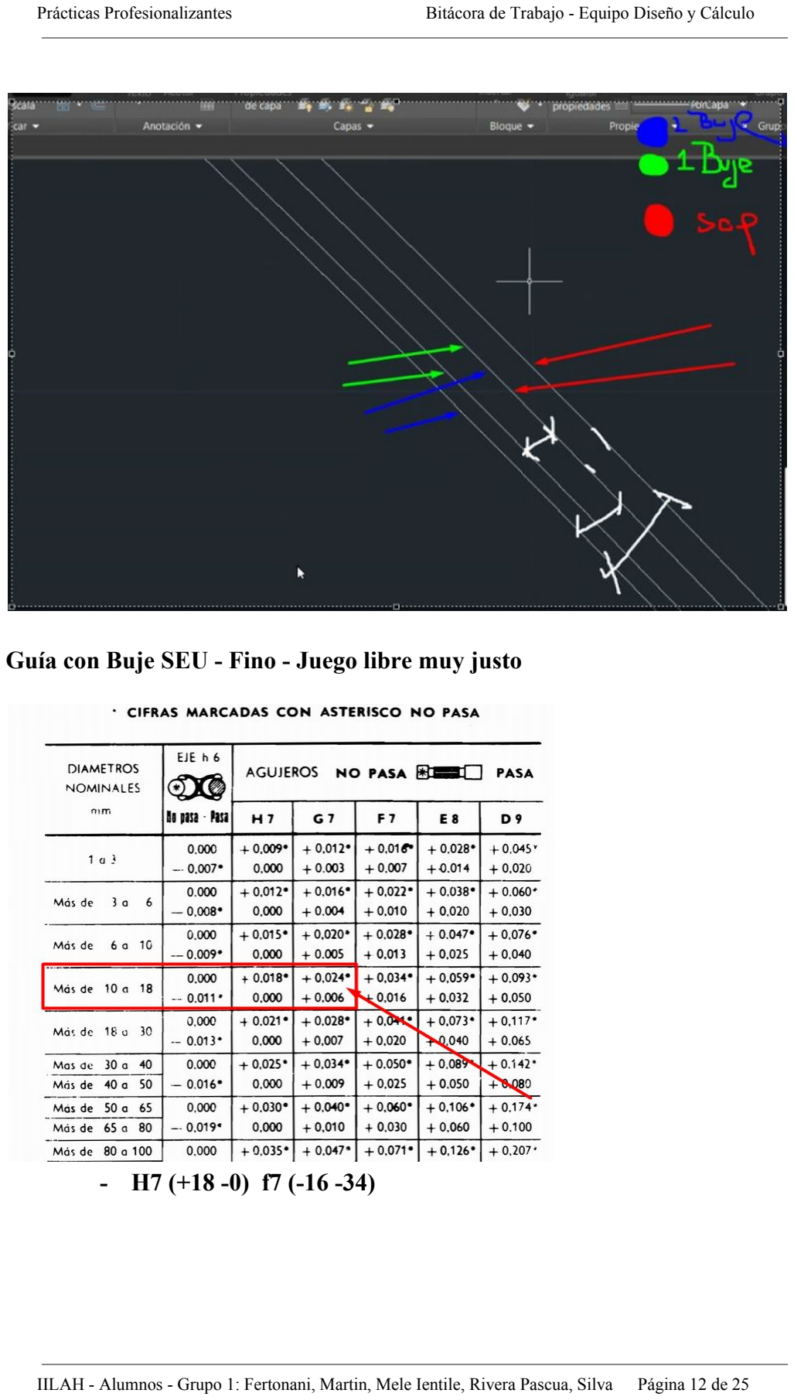
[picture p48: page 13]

## Guía con Buje SEU - Fino - Juego libre muy justo

- H7 (+18 -0) f7 (-16 -34)

IILAH - Alumnos - Grupo 1: Fertonani, Martin, Mele Ientile, Rivera Pascua, Silva Página 12 de 25

## NUEVO AJUSTE SEGÚN GUÍA CROMADA Y RECTIFICADA

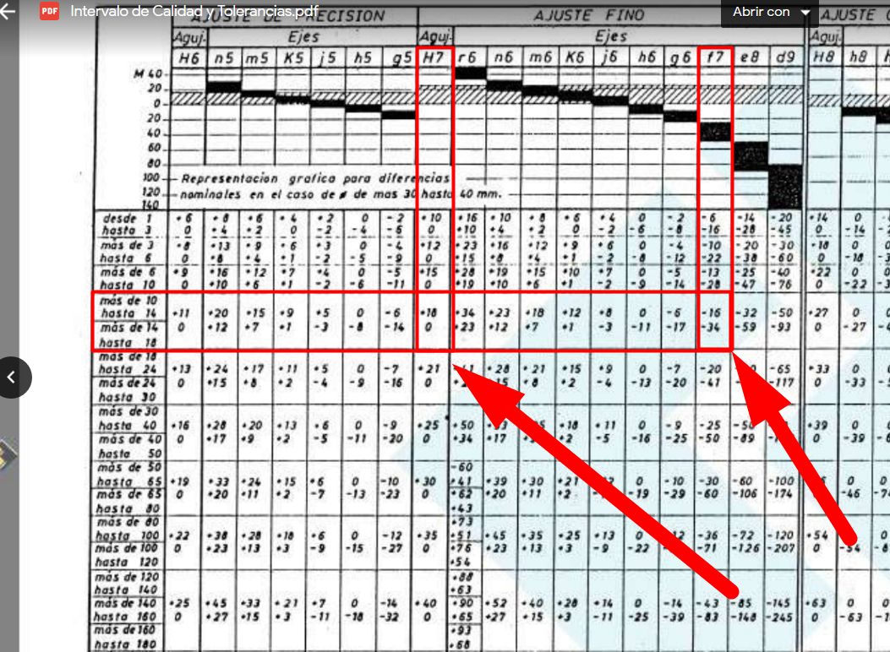
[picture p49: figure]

## f7 -> Guía del padre de mele (cromada y rectificada) -> f7=-16; -34 →

-20; -30
El agujero? Bueno, ni idea de donde sale. Tomamos H7 y rezamos.

## Entonces: Agujero H7 -> 18; 0 -> 20; 0

## La nueva tolerancia del agujero interno del buje queda así:

40; 0

IILAH - Alumnos - Grupo 1: Fertonani, Martin, Mele Ientile, Rivera Pascua, Silva Página 13 de 25

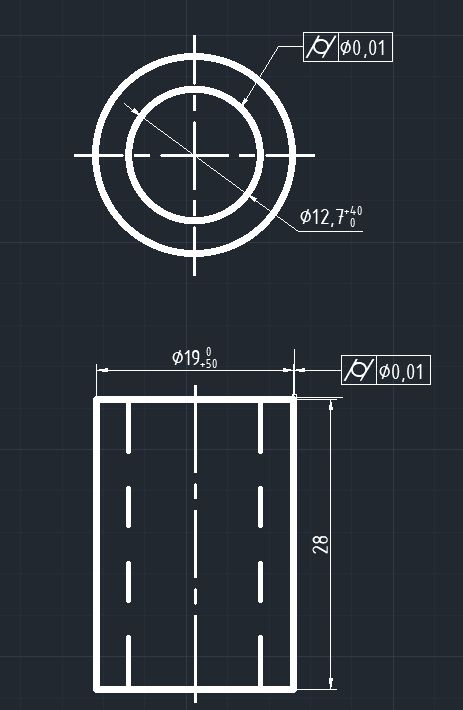
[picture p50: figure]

## Tornillo con Buje SAU - Ajuste Fino - Juego fuerte

IILAH - Alumnos - Grupo 1: Fertonani, Martin, Mele Ientile, Rivera Pascua, Silva Página 14 de 25

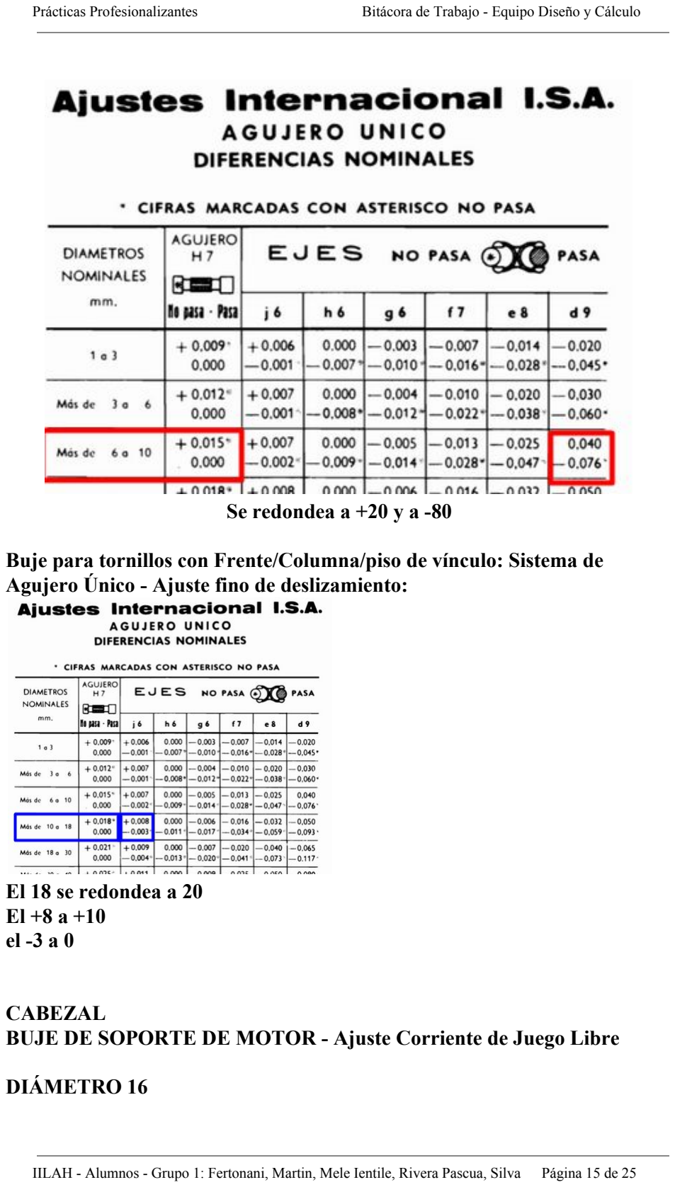
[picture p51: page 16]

## Se redondea a +20 y a -80

## Buje para tornillos con Frente/Columna/piso de vínculo: Sistema de Agujero Único - Ajuste fino de deslizamiento:

## El 18 se redondea a 20 El +8 a +10 el -3 a 0

## CABEZAL BUJE DE SOPORTE DE MOTOR - Ajuste Corriente de Juego Libre

## DIÁMETRO 16

IILAH - Alumnos - Grupo 1: Fertonani, Martin, Mele Ientile, Rivera Pascua, Silva Página 15 de 25

## aguj único. H8 = +27 -0 -> Se redondea a +30; 0 f8 = -16 -43 -> Se redonde a -20 -40

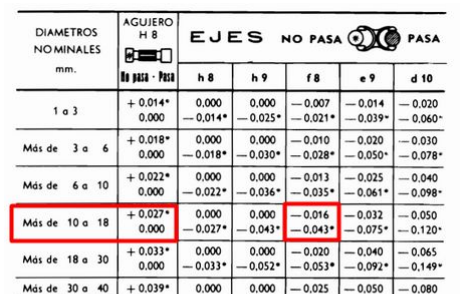
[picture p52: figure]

## LA CHAPA QUE GUÍA EL CABLE DEL MOTOR DC LA TENEMOS QUE LIMAR PARA QUE NO ROMPA EL CABLE Y LE TENEMOS QUE AGRANDAR EL AGUJERO PA’ QUE QUEDE COMO UN ÓVALO

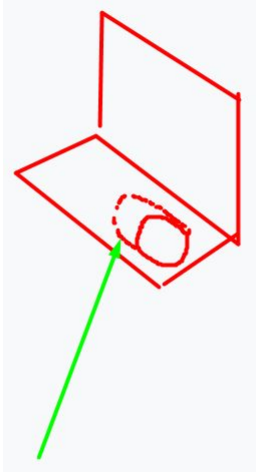
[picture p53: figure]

IILAH - Alumnos - Grupo 1: Fertonani, Martin, Mele Ientile, Rivera Pascua, Silva Página 16 de 25

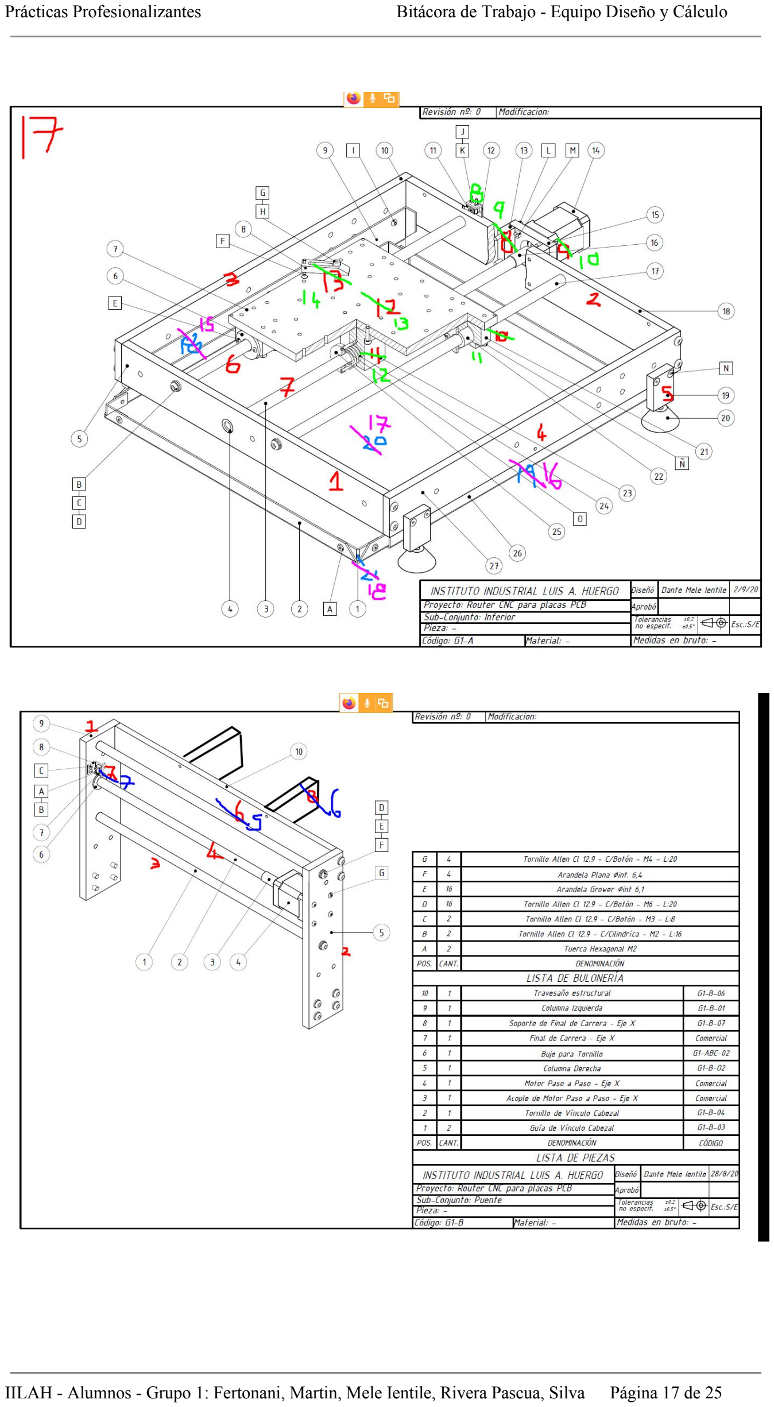
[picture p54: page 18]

IILAH - Alumnos - Grupo 1: Fertonani, Martin, Mele Ientile, Rivera Pascua, Silva Página 17 de 25

## AAAAAAAA

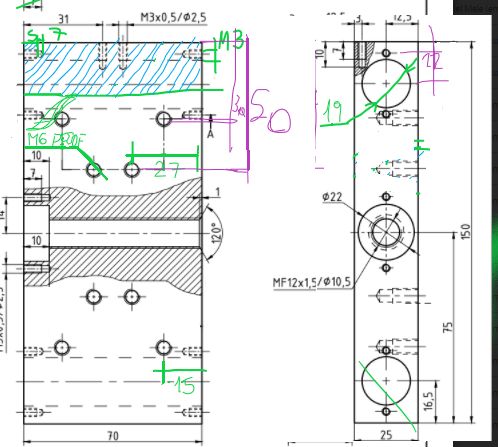
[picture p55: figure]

## Ojo que los roscados largos (acople de soporte de motor por ejemplo) pueden llegar a necesitar una mecha del otro lado por el largo del macho para roscar

Medias en bruto de la agujereadora: - Acero SAE 1020 Trefilado - D:25,4mm - Al 2005 - Aluminio 50,8 x 50,8 - SAE 1010 D: 44,45 - Al 2005A - 50,8 x 50,8 - Latón - 50,8 x 50,8 - Latón B 16 D: 44,45 - Acero 12L14 Trefilado - D: 22,22 - Al 2005A - D:60 - Al 2005A - 50 x 10 - SAE 1010 - D:10 - Aluminio 2005A - D:20x90 - SAE 12L14 - D: 12 - Latón - Trefilado -> 25,4x10

IILAH - Alumnos - Grupo 1: Fertonani, Martin, Mele Ientile, Rivera Pascua, Silva Página 18 de 25

## CARCASA (24/9/2020)

Lista A
- Potenciómetro de motor a la derecha (con su chapa) -> Listo
- Mini Cable Canal de alterna y para USB B
- Chapa de refrigeración (hacerla entera y colocar tornillos) ->Listo
- Agujeros para componentes y tira led en cielo raso
- Ojo que coinciden en el cable canal de AC
- Agujeros para ventiladores (sujeción como para el aire) -> Listo
- Agujeros para cables del reed switch y para cable de tira led -> Listo
- Agujero para toma a tierra -> Listo
- Agujero y ranura para chapa e imanes (en frente carcasa y lateral derecho carcasa) -> No existen
- Revisar agujeros para cables en chapon -> Listo
- Reed switch:
- Revisar la colocación
- Hacer protector
- Colocar protector
- Agregar toma a tierra de tercer pata a soporte para culata carcasa -> Listo
- Tornillos para usb - b -> Listo
- Averiguar agujeros de las fuentes
LISTA B
- Colocar BUSCAR soporte para LED (portaled metálico) -> Listo
- TODOS los catálogos (PRIMERO EL DE LAS FUENTES y PARADA DE EMERGENCIA)
- Borrador de topografico

INVENTOR
1. Agujeros de electrónica (potenciómetro, led indicador, etc) -> Listo
2. Agujeros para sujetar componentes (comparar con catálogos electrónicos)
3. Agujeros secundarios / sujección (Lista A)

ELECTRÓNICA
1. Electronica hace LISTA B

AutoCAD
A. Terminar piezas empezadas
2. Empezar con las nuevas piezas (catálogos, bisagras, etc.)
3. Terminar con chapas difíciles (chapon, cielo raso)

Informe de estado:
-Planos: Entregar carcasa y corregir las demas devoluciones
-Cotización y compra de materiales: Charla/consulta con profes para determinar que materiales nos da el colegio, y terminar de cotizar los materiales y hacer los pedidos.
-Diagramas de operaciones
-Lista:
1. Revisar los diagramas hechos
2. Entregar/consultar diagramas con los profes
3. Corregir los diagramas que estén mal

IILAH - Alumnos - Grupo 1: Fertonani, Martin, Mele Ientile, Rivera Pascua, Silva Página 19 de 25

4. Empezar con los diagramas que falten

Ojo al piojo!
Van:
- https://grabcad.com/library/sts-cam-locks
- https://grabcad.com/library/cam-lock-5
- https://grabcad.com/library/25mm-camlock-1

Son Step:
- https://grabcad.com/library/mk-lock-key-cabinet-1
- https://grabcad.com/library/lock-yale-6700-1
- https://grabcad.com/library/quarter-turn-panel-lock-1

No son STEP:
- https://grabcad.com/library/lock-with-key
- https://grabcad.com/library/ctk-3-4-1
- https://grabcad.com/library/godrej-lock-1
- https://grabcad.com/library/key-lock-5

# LISTA General Máquina 4/10

- Agujeros en fuentes
- Colocar fuentes (espacidores y tornillos)
- Alinear Placas
- Colocar placas (espaciadores y tornillos)
- Cablecanales “reales”
- Colocar mini cable canal
- Sujetar cablecanales
- Sujetar Soporte para Tira LED
- Sujetar correctamente Carcasa Derecha de Reed Switch

Diseño
- Colocar Cerraduras
- Colocar tope de resina
- Solucionar lo de la Puerta de Inspección

Admin:
- Resumir cada componente en planilla elect
- Resumir cada tornillo de elect
- Revisar tornillos generales de máquina

CERRADURAS DE LEVA

Tärken es re comun
vamos a usar una de diametro 18, largo 25 (asi es la de inventor)
Nuestro proveedor de mercadolibre tiene otra marca, pero deberían ser las mismas medidas

(catálogo sacado de otro proveedor)

IILAH - Alumnos - Grupo 1: Fertonani, Martin, Mele Ientile, Rivera Pascua, Silva Página 20 de 25

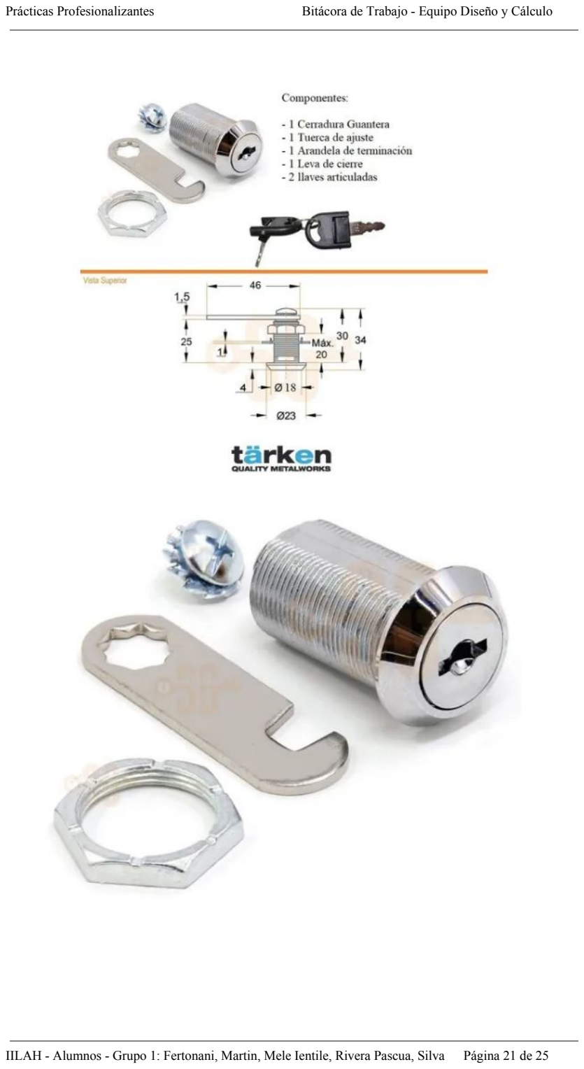
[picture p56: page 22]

IILAH - Alumnos - Grupo 1: Fertonani, Martin, Mele Ientile, Rivera Pascua, Silva Página 21 de 25

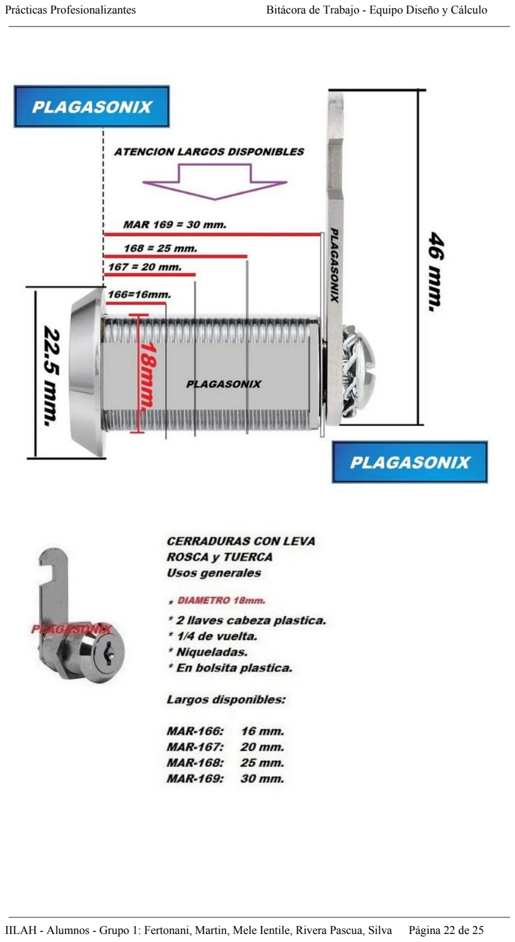
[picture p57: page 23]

IILAH - Alumnos - Grupo 1: Fertonani, Martin, Mele Ientile, Rivera Pascua, Silva Página 22 de 25

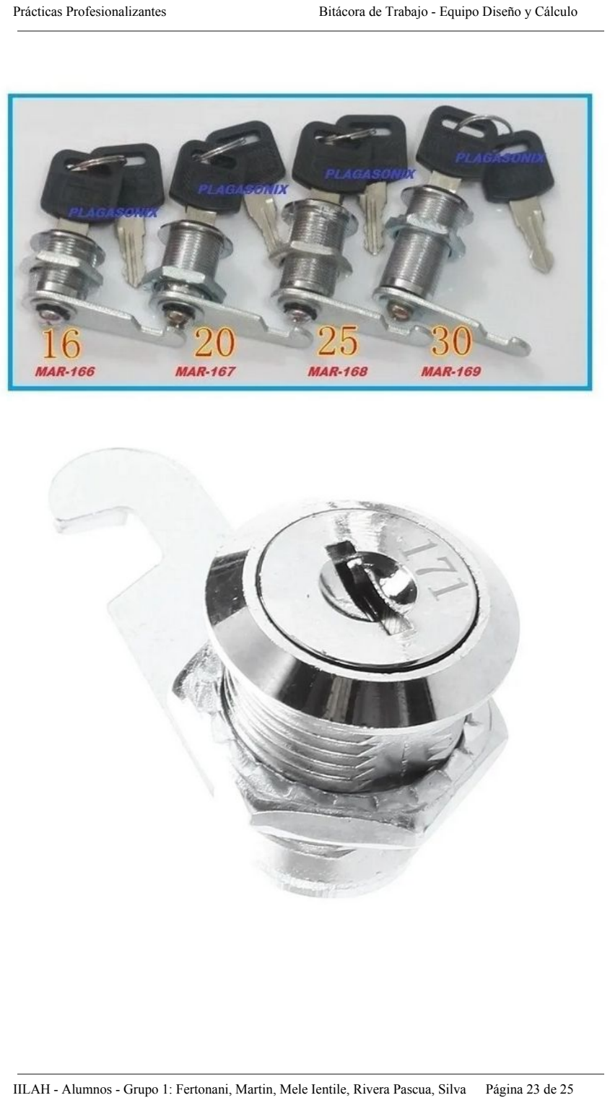
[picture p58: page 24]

IILAH - Alumnos - Grupo 1: Fertonani, Martin, Mele Ientile, Rivera Pascua, Silva Página 23 de 25

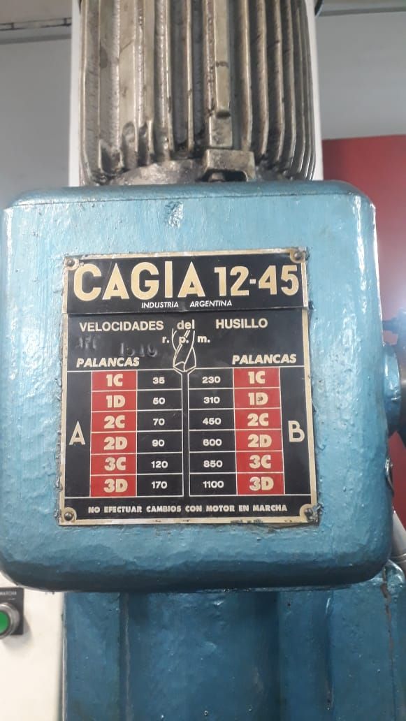
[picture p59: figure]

IILAH - Alumnos - Grupo 1: Fertonani, Martin, Mele Ientile, Rivera Pascua, Silva Página 24 de 25

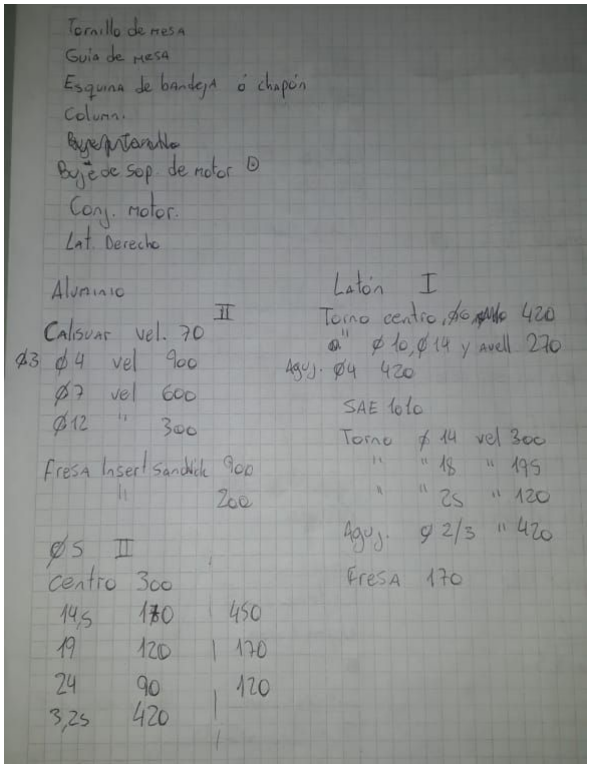
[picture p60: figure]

IILAH - Alumnos - Grupo 1: Fertonani, Martin, Mele Ientile, Rivera Pascua, Silva Página 25 de 25

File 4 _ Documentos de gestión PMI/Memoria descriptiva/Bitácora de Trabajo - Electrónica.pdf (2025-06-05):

# Bitácora de Trabajo:

# Equipo Electrónica

Grupo 1.

## - Docentes:

## - Osvaldo P. Ivani - Sebastián Amago Prato - Martín A. Ricciardelli - Juan Martín Hermida

## - Estudiantes: - Dante G. Mele Ientile (Project Manager) - León A. Martin - Hernán A. Silva - Nicolás L. Fertonani - Laureano M. Rivera Pascua

## - Curso: 4

## to Año Ciclo Superior - Electromecánica

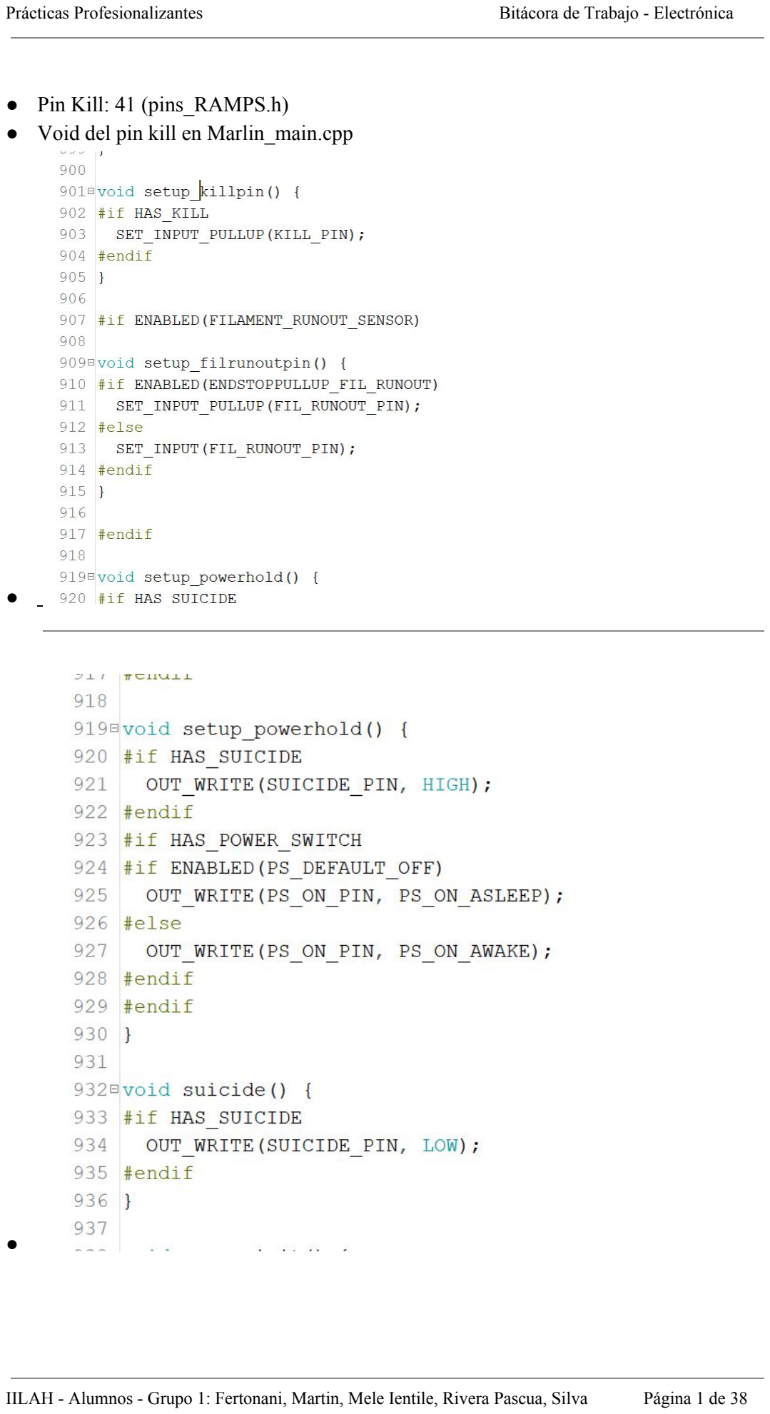
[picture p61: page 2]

Prácticas Profesionalizantes | Bitácora de Trabajo - Electrónica
- Pin Kill: 41 (pins_RAMPS.h)
- Void del pin kill en Marlin_main.cpp

●

●

IILAH - Alumnos - Grupo 1: Fertonani, Martin, Mele Ientile, Rivera Pascua, Silva Página 1 de 38

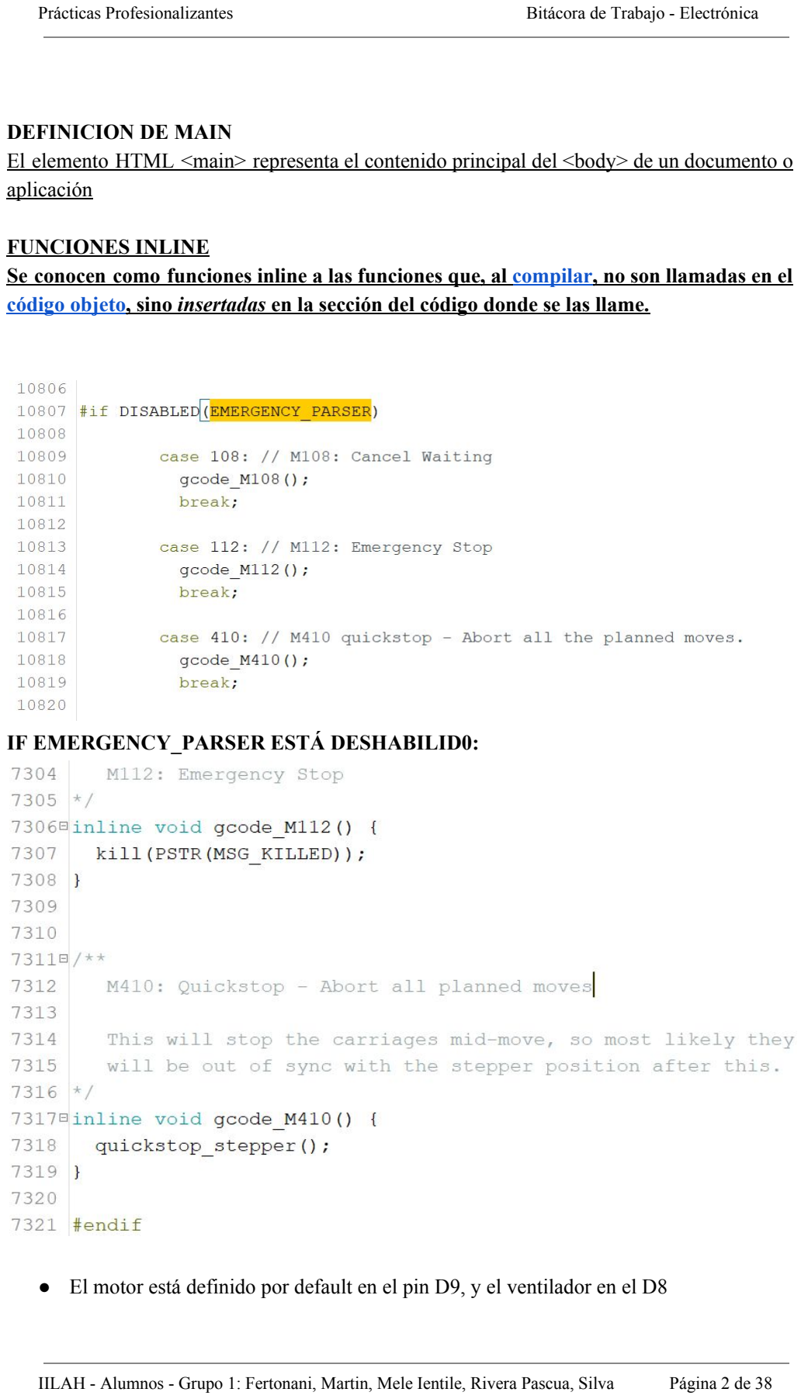
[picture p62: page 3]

DEFINICION DE MAIN
El elemento HTML <main> representa el contenido principal del <body> de un documento o aplicación

FUNCIONES INLINE
Se conocen como funciones inline a las funciones que, al compilar, (https://es.wikipedia.org/wiki/Compilador) no son llamadas en el código objeto, (https://es.wikipedia.org/wiki/C%C3%B3digo_objeto) sino insertadas en la sección del código donde se las llame.

IF EMERGENCY_PARSER ESTÁ DESHABILID0:

- El motor está definido por default en el pin D9, y el ventilador en el D8

IILAH - Alumnos - Grupo 1: Fertonani, Martin, Mele Ientile, Rivera Pascua, Silva Página 2 de 38

define | MSG_ERR_KILLED | "Printer

# halted. kill() called!"

is used only in this method

void kill(const char* lcd_msg) {

SERIAL_ERROR_START;

SERIAL_ERRORLNPGM(MSG_ERR_KILLED);

# if ENABLED(ULTRA_LCD)

kill_screen(lcd_msg);

# else

UNUSED(lcd_msg);

# endif

delay(500); // Wait a short time

cli(); // Stop interrupts

thermalManager.disable_all_heaters();

disable_all_steppers();

# if HAS_POWER_SWITCH

SET_INPUT(PS_ON_PIN);

# endif

IILAH - Alumnos - Grupo 1: Fertonani, Martin, Mele Ientile, Rivera Pascua, Silva Página 3 de 38

suicide();

while (1) {

# if ENABLED(USE_WATCHDOG)

- watchdog_reset();
#endif

} // Wait for reset

}

Problem is that it can be called from many places:

1070: if (strcmp(command, "M112") == 0) kill(PSTR(MSG_KILLED));

/**

- Manage several activities:
- Check for Filament Runout
- Keep the command buffer full
- Check for maximum inactive time between commands
- Check for maximum inactive time between stepper commands
- Check if pin CHDK needs to go LOW
- Check for KILL button held down
- Check for HOME button held down
- Check if cooling fan needs to be switched on
- Check if an idle but hot extruder needs filament extruded (EXTRUDER_RUNOUT_PREVENT)
/
void manage_inactivity(bool ignore_stepper_queue/=false*/) { .....
9924: if (max_inactive_time && ELAPSED(ms, previous_cmd_ms + max_inactive_time)) kill(PSTR(MSG_KILLED));

which is probably turning of after idlle...

Then there are the temperature safes (can you recompile without the temperature safety to eliminate this code?

IILAH - Alumnos - Grupo 1: Fertonani, Martin, Mele Ientile, Rivera Pascua, Silva Página 4 de 38

if

# DISABLED(BOGUS_TEMPERATURE_ FAILSAFE_OVERRIDE)

- if (!killed) {
- Running = false;
- killed = true;
- kill(lcd_msg);
- }
- else
disable_all_heaters(); // paranoia

# endif

if

# ENABLED(TEMP_SENSOR_1_AS_RED UNDANT)

if (e > HOTENDS)

# else

if (e >= HOTENDS)

# endif

- {
- SERIAL_ERROR_START;
- SERIAL_ERROR((int)e);
- SERIAL_ERRORLNPGM(MSG_INVALID_EXTRUDER_NUM);
- kill(PSTR(MSG_KILLED));
- return 0.0;
}

IILAH - Alumnos - Grupo 1: Fertonani, Martin, Mele Ientile, Rivera Pascua, Silva Página 5 de 38

There is one when handling SD files (but you said it happens even without)

if (isFileOpen()) { //replacing current file by new file, or subfile call

if (push_current) {

if (file_subcall_ctr > SD_PROCEDURE_DEPTH - 1) {

SERIAL_ERROR_START;

SERIAL_ERRORPGM("trying to call sub-gcode files with too many levels. MAX level is:");

SERIAL_ERRORLN(SD_PROCEDURE_DEPTH);

kill(PSTR(MSG_KILLED));

return;

}

Then there is watch dog

// Watchdog timer interrupt, called if main program blocks >1sec and manual reset is enabled.
if

# ENABLED(WATCHDOG_RESET_MAN UAL)

ISR(WDT_vect) {

SERIAL_ERROR_START;

SERIAL_ERRORLNPGM("Something is wrong, please turn off the printer.");

kill(PSTR("ERR:Please Reset")); //kill blocks //16 characters so it fits on a 16x2 display

while (1); //wait for user or serial reset

}

IILAH - Alumnos - Grupo 1: Fertonani, Martin, Mele Ientile, Rivera Pascua, Silva Página 6 de 38

# endif //WATCHDOG_RESET_MANUAL

It needs to be one of these, disable one by one each of them in the firmware with the Configuration.h to know which it is. It could even be even M112 kind, like emergency stop, it could be triggered by both min and max endstops triggered at the same time (that could happen if contacts got dirty, or the connector itself and is leaking current into wrong pin on the mcu).

If you have kill button then probably this is enabled as well

# if HAS_KILL

- // Check if the kill button was pressed and wait just in case it was an accidental
- // key kill key press
- // -------------------------------------------------------------------------------
- static int killCount = 0; // make the inactivity button a bit less responsive
- const int KILL_DELAY = 750;
- if (!READ(KILL_PIN))
- killCount++;
- else if (killCount > 0)
- killCount--;
●
- // Exceeded threshold and we can confirm that it was not accidental
- // KILL the machine
- // ----------------------------------------------------------------
if (killCount >= KILL_DELAY) kill(PSTR(MSG_KILLED));

# endif

So then any dirt or interference around that pin can trigger it by accident. Hope something will help you find out what the cause is.

- PASOS | PARA | MARLIN:
https://marlinfw.org/docs/development/coding_standards.html

IILAH - Alumnos - Grupo 1: Fertonani, Martin, Mele Ientile, Rivera Pascua, Silva Página 7 de 38

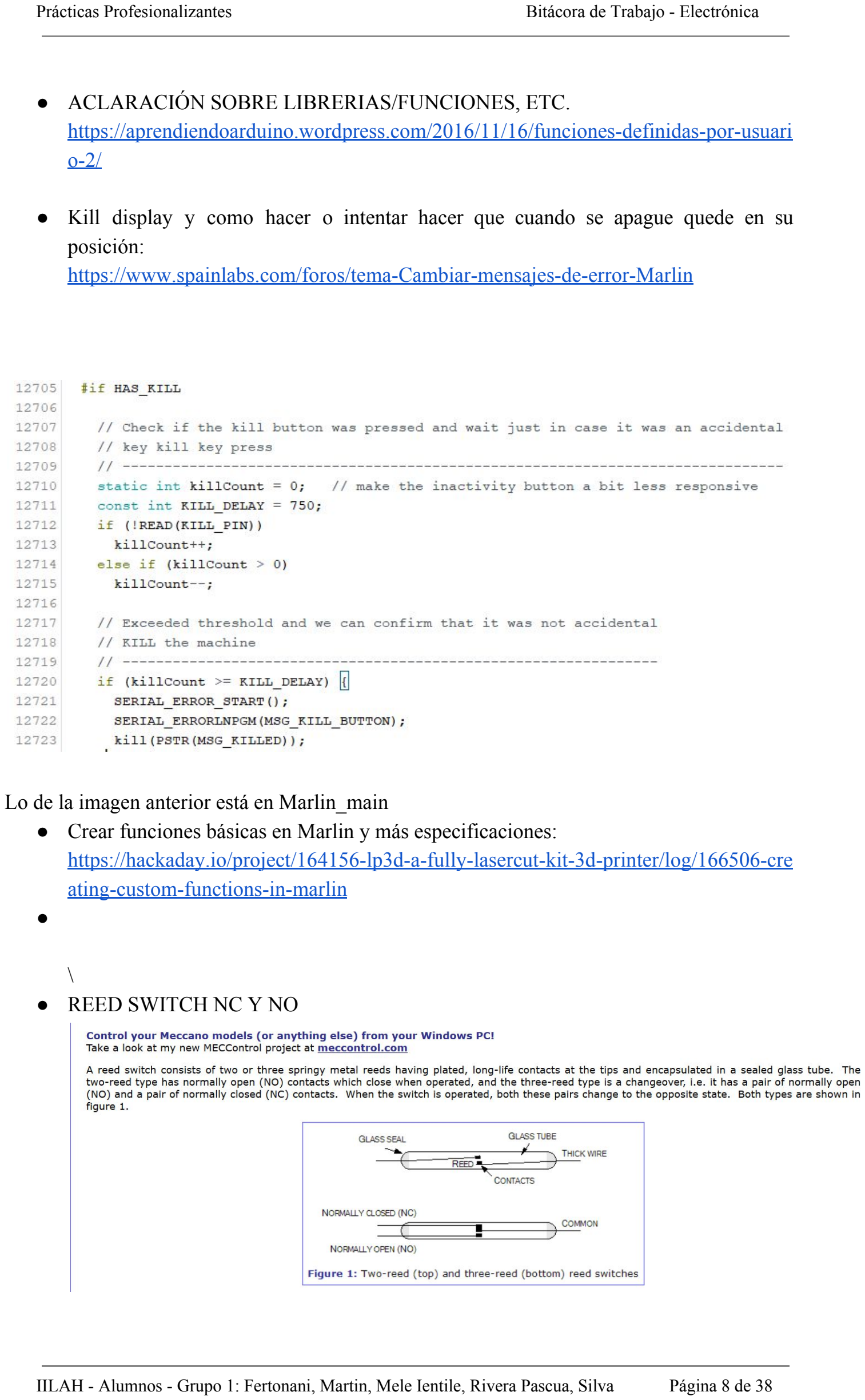
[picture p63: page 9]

- ACLARACIÓN SOBRE LIBRERIAS/FUNCIONES, ETC. https://aprendiendoarduino.wordpress.com/2016/11/16/funciones-definidas-por-usuario-2/ (https://aprendiendoarduino.wordpress.com/2016/11/16/funciones-definidas-por-usuario-2/)
- Kill display y como hacer o intentar hacer que cuando se apague quede en su posición:
https://www.spainlabs.com/foros/tema-Cambiar-mensajes-de-error-Marlin

Lo de la imagen anterior está en Marlin_main
- Crear funciones básicas en Marlin y más especificaciones: https://hackaday.io/project/164156-lp3d-a-fully-lasercut-kit-3d-printer/log/166506-cre ating-custom-functions-in-marlin (https://hackaday.io/project/164156-lp3d-a-fully-lasercut-kit-3d-printer/log/166506-creating-custom-functions-in-marlin)
●

\
- REED SWITCH NC Y NO

IILAH - Alumnos - Grupo 1: Fertonani, Martin, Mele Ientile, Rivera Pascua, Silva Página 8 de 38

- G-codes sender y más
https://reprap.org/wiki/PCB_Milling#Software_suites
- Mapeo de Alturas con Marlin: https://martinvb.com/wp/using-marlins-auto-leveling-for-pcb-milling/
- Para mañana:
https://reprap.org/forum/read.php?131,554184https://forum.v1engineering.com/t/pcb-milling-bed-levelling/8138/4
- Marlin para torpes - Linked https://es.slideshare.net/xprado/marlin-paratorpes102
- Guía completa: Configurar Marlin 2.0.x desde cero y no morir en el intento https://3dwork.io/configurar-marlin-2-0-x-desde-cero/
- Firmware definitivo (Marlin) https://www.zonamaker.com/impresion-3d/crea-impresora/14-crea-imp-firma ware-marlin (https://www.zonamaker.com/impresion-3d/crea-impresora/14-crea-imp-firmaware-marlin)
- Diagrama fuente switching https://www.diarioelectronicohoy.com/blog/imagenes/2010/11/TO-220AB.gif

●

IILAH - Alumnos - Grupo 1: Fertonani, Martin, Mele Ientile, Rivera Pascua, Silva Página 9 de 38


●

IILAH - Alumnos - Grupo 1: Fertonani, Martin, Mele Ientile, Rivera Pascua, Silva Página 10 de 38

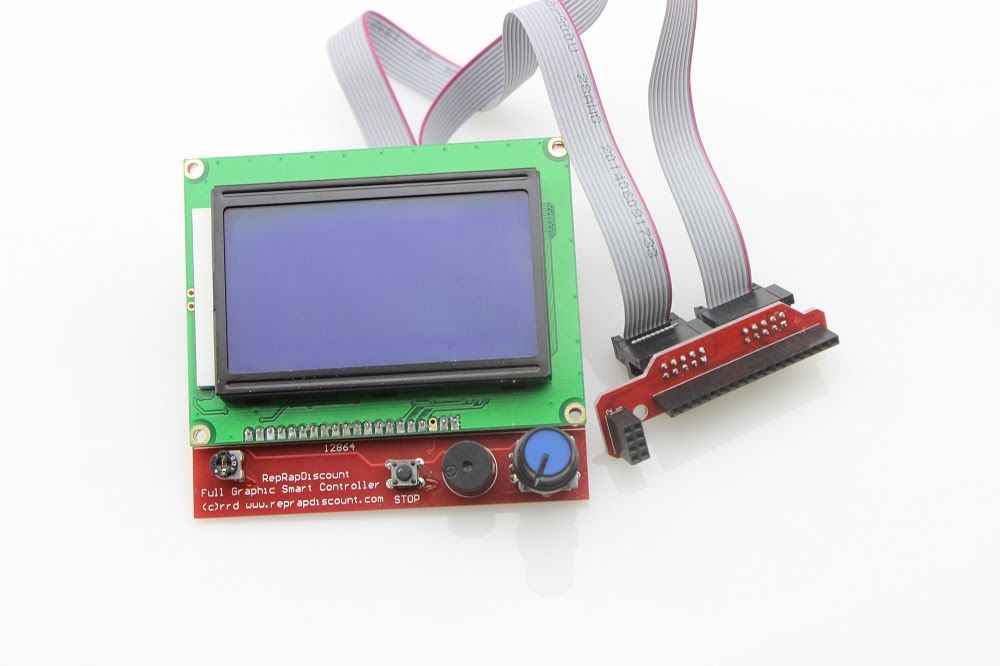
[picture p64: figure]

IILAH - Alumnos - Grupo 1: Fertonani, Martin, Mele Ientile, Rivera Pascua, Silva Página 11 de 38

IILAH - Alumnos - Grupo 1: Fertonani, Martin, Mele Ientile, Rivera Pascua, Silva Página 12 de 38

## https://reprap.org/wiki/CNC_Gcode_controller

## VIDEOS SOBRE EL CONTROLADOR CNC-GCODE: https://www.youtube.com/watch?v=xxbBipRvp5I&t=1114s https://www.youtube.com/watch?v=Y12oszEqwF8

## Blogs sobre la app: http://diwo.bq.com/cnc-gcode-controller-instalacion-y-uso/

Blog sobre GCODE: https://gcodetutor.com/cnc-machine-training/cnc-g-codes.html https://gcodetutor.com/articles.html https://gcodetutor.com/cnc-machine-training/cnc-g-codes.html https://gcodetutor.com/fanuc-training-course/cnc-mill-progra mming.html (https://gcodetutor.com/fanuc-training-course/cnc-mill-programming.html) https://gcodetutor.com/gcode-tutorial/cnc-m-codes.html https://tormach.com/temporary-work-offsets-g92-g92-1-g92-2 -and-g92-3 (https://tormach.com/temporary-work-offsets-g92-g92-1-g92-2-and-g92-3)

## GCODE - MARLIN: https://marlinfw.org/docs/gcode/G092.html https://marlinfw.org/docs/gcode/G092.html

## MAS DE LO MISMO

https://www.haascnc.com/service/codes-settings.type=gcode.machine=mill.value=G28.html (https://www.haascnc.com/service/codes-settings.type=gcode.machine=mill.value=G28.html)

IILAH - Alumnos - Grupo 1: Fertonani, Martin, Mele Ientile, Rivera Pascua, Silva Página 13 de 38

## https://machmotion.com/cnc-info/g-code.html https://books.google.com.ar/books?id=D4x8AwAAQBAJ&pg =PT278&lpg=PT278&dq=parameters+5161-5166&source=bl &ots=L_EJJrix3Z&sig=ACfU3U1WRtkiTr9Qp7rVWCB2XO Vr2aQogg&hl=en&sa=X&ved=2ahUKEwjJqtXr7vzpAhWW HbkGHXYRCRkQ6AEwAHoECAkQAQ#v=onepage&q=ho

me&f=false (https://books.google.com.ar/books?id=D4x8AwAAQBAJ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)

## HABER, COMO SE HACE LA PUESTA A CERO DE LA MAQUINA

## - Primero, no te hagas el tonto y pone en la pestaña “Advanced Options” de la mejor app del mundo (CNC Gcode Controller) Homing para que la herramienta se vaya hasta los finales de carrera y se establezca de esta forma el cero

máquina.

## - Pasaste lo anterior?

- Si!!
- Muy bien!, pero te falta el 0 pieza nene.

## - Uy, como hago eso? - Primero no grites, lo que tenés que hacer es poner en “Delta” la distancia en donde queres que este tu cero pieza. Y una vez que estés en esa posición te vas a "Set Position" y pones X,Y y Z todo en 0 - Uhh, no se bien donde tiene que ir

- Tranquilo, tenemos todo preparado para tontos como vos,

## esto es APB. Anda a la pestaña “Simple Controls” y movete

IILAH - Alumnos - Grupo 1: Fertonani, Martin, Mele Ientile, Rivera Pascua, Silva Página 14 de 38

## hasta que masomenos a ojo veas que la herramienta está en el

borde izquierdo de la placa pcb.

## - OKOK

- Como okok, te acabo de salvar la vida.

## - Bueeee tranquilo - Ya ta? - Si, ya fui a donde maso quiero que vaya - Bien, hace lo de "Set Position", todo te tengo que decir viejo? - Disculpá, ya ta - Bueno listo, que mas queres, nos vemos en el próximo tutorial. Saludos!

## El chino conecta el motor a D9 - Mos si es que el que viene se prende fuego https://reprapworld.com/products/electronics/component

s/mosfet_s/mosfet_n_ch_30v_150a_irlb8743pbf/ (https://reprapworld.com/products/electronics/components/mosfet_s/mosfet_n_ch_30v_150a_irlb8743pbf/)

## Conector interlock C14 CHASSIS

IILAH - Alumnos - Grupo 1: Fertonani, Martin, Mele Ientile, Rivera Pascua, Silva Página 15 de 38

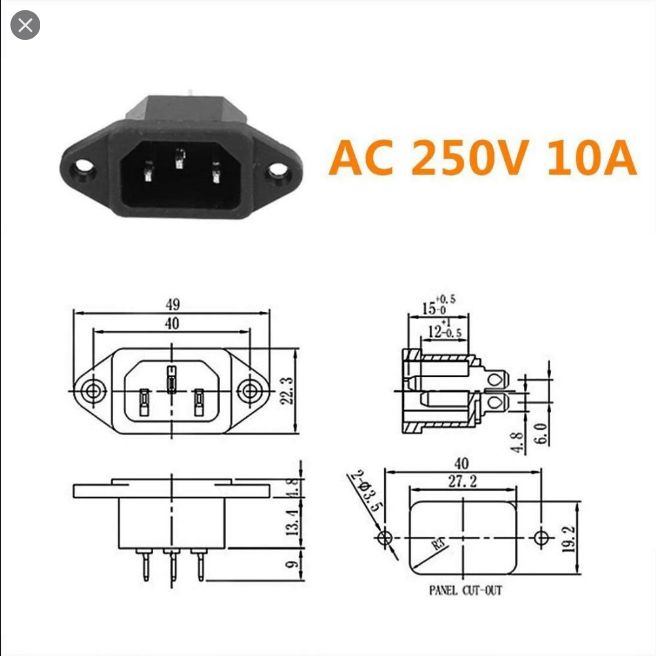
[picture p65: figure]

## http://www.sycelectronica.com.ar/articulo.php?codigo=T ECLA-TR12-N (http://www.sycelectronica.com.ar/articulo.php?codigo=TECLA-TR12-N)

## - Vídeo de explicación boost: https://www.youtube.com/watch?v=6WwCqxSaF_w https://www.youtube.com/watch?v=9tQR-i7b6WA https://www.youtube.com/watch?v=RRY0R2vqKIE https://www.youtube.com/watch?v=RRY0R2vqKIE

IILAH - Alumnos - Grupo 1: Fertonani, Martin, Mele Ientile, Rivera Pascua, Silva Página 16 de 38

## http://www.reprap.com/wiki/Heated_Bed_MOSFET_Po

wer_Expansion_Module (http://www.reprap.com/wiki/Heated_Bed_MOSFET_Power_Expansion_Module)

Tema MKS MOS - DISIPACIÓN DE CALOR,

## FUENTE DE 24 V - APROVECHAMIENTO MÁXIMO DE POTENCIA

## https://github.com/Aus3D/RUMBA-Plus/issues/7 -> Hablan de cuanto se banca el MOS de Ramps

## Video donde explica todo lo relacionado con la fuente de 24V y el MKS MOS https://www.youtube.com/watch?v=6WwCqxSaF_w&lis t=PLBd0pmvp-_tDTLAkC3afL6U3rJCrxE6eh&index=2

&t=1473s (https://www.youtube.com/watch?v=6WwCqxSaF_w&list=PLBd0pmvp-_tDTLAkC3afL6U3rJCrxE6eh&index=2&t=1473s)

## TEMA MOTORES PASO A PASO Y SUS CABLES: - Twist the wires (enrosca los cables del pap para disminuir la inducción - 3 metros de cable no pasa na!

- Se pueden enrroscar por bobina en lugar de todos juntos.

## Así se hace en los servomotores industriales - En cuanto a la vibración y al ruido de los motores, se colocan unos dampers

IILAH - Alumnos - Grupo 1: Fertonani, Martin, Mele Ientile, Rivera Pascua, Silva Página 17 de 38

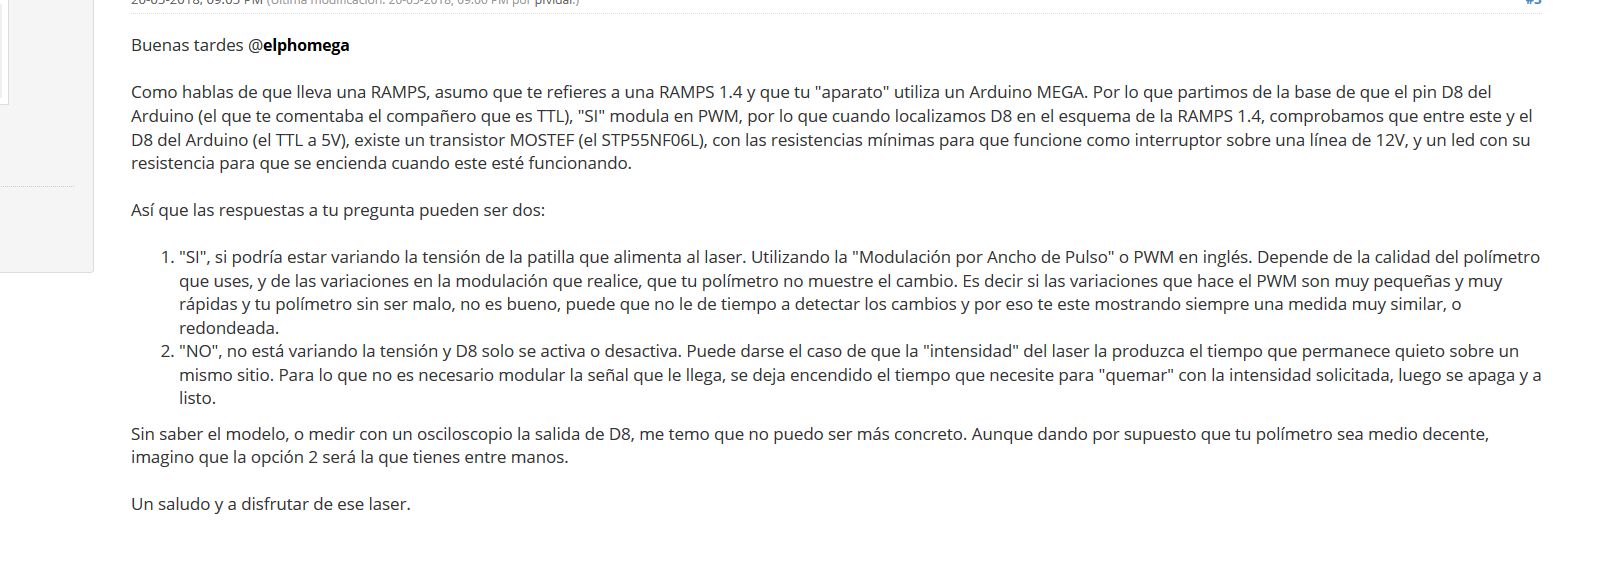
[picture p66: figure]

- Conexión de cable apantallado: Como conectarlo, porqué, etc.

## https://www.cemdal.com/2020/01/23/las-conexiones-a-m

asa-de-un-cable-apantallado-en-uno-o-dos-lados/ (https://www.cemdal.com/2020/01/23/las-conexiones-a-masa-de-un-cable-apantallado-en-uno-o-dos-lados/)

## - OJO QUE PARA EL FINAL DE CARRERA HAY QUE COLOCAR LAS RESISTENCIAS PULL DOWN Y PULL UP EN EL MARLIN

## - Makerbots tiene planitos de las cosas

## - El final de carrera lo usamos como viene pero de forma empírica le metemos un pequeño filtro y un pull down o

pull up si es necesario.

IILAH - Alumnos - Grupo 1: Fertonani, Martin, Mele Ientile, Rivera Pascua, Silva Página 18 de 38

●


## No hace falta usar dumpers o smoothers ya que en la práctica

no hacen diferencia, usar mayor cantidad de micropasos. ------------------------------------------------------------------------------------------------------------------------------------------------------------------------------------------------------------------------------------

## Etapa 4

## https://protosupplies.com/product/usb-type-b-female-to-2-54

mm-header-breakout/ (https://protosupplies.com/product/usb-type-b-female-to-2-54mm-header-breakout/)

IILAH - Alumnos - Grupo 1: Fertonani, Martin, Mele Ientile, Rivera Pascua, Silva Página 19 de 38


IILAH - Alumnos - Grupo 1: Fertonani, Martin, Mele Ientile, Rivera Pascua, Silva Página 20 de 38


IILAH - Alumnos - Grupo 1: Fertonani, Martin, Mele Ientile, Rivera Pascua, Silva Página 21 de 38


## Circuito de Dimmer

IILAH - Alumnos - Grupo 1: Fertonani, Martin, Mele Ientile, Rivera Pascua, Silva Página 22 de 38


Circuito Interno de LM555


Funcionamiento:
Por un lado, el circuito Integrado 555 (timer o compraador, ni idea) comprará (gracias a sus comparadores, obvio) la tensión de entrada de a tercios. Es decir, evaluará si en el pin Thr existe más ⅔ de la tensión de entrada, es decir, más de 8V. Y en el pin Tri evaluará si existe menos de ⅓, es decir, menos de 4V.
En un primer instante, el capacitor estará descargado y la corriente de carga circulará por un circuito RC compuesto por la resistencia de 1k, el valor resistivo del potenciómetro, el diodo D1 y, por su puesto, el Capacitor C1. Evidentemente, como el capacitor se encuentra

IILAH - Alumnos - Grupo 1: Fertonani, Martin, Mele Ientile, Rivera Pascua, Silva Página 23 de 38 descargado, en el comparador U2 la tensión será mayor en el pin + que en él - y, por lo tanto, habrá un 1 a la salida del 555
A medida que el capacitor se carga, la tensión de pin + del comparador U1 aumentará y será mayor a la tensión en el pin - del mismo. Esto generará que a la salida Q exista un 0 y, como consecuencia, la salida Q negada tenga un 1, lo que exitará la base del transistor de descarga interno del 555
EVIDENTEMENTE, LA BASE DEL TRANSISTOR DE DESCARGA DEBE TENER UNA RESISTENCIA LIMITADORA PQ SINO SE ROMPE TODO. Entonces, dependiendo del valor resistivo que posea el potenciómetro, la constante de tiempo del capacitor tendrá un valor distinto, es decir, al variar el potenciómetro se varía el tiempo de carga y de descarga del capacitor. Como cada curva está asociada a un nivel alto y a un nivel bajo, dependiendo de la posición del potenciómetro modulamos el ancho de pulso. El potenciómetro R2 nos sirve para poder ajustar el tiempo de duración del pulso, o, el ancho del pulso, debido a esto se obtiene una señal PWM (Modulación por ancho de pulso). El mosfet IRFZ24N funciona como una “llave On/Off” adecuada para manejar los niveles altos de corriente requeridos por la tira led.

# Colocación de los disipadores de los driverso


IILAH - Alumnos - Grupo 1: Fertonani, Martin, Mele Ientile, Rivera Pascua, Silva Página 24 de 38

BOOST STEP UP:
Todo micro:
https://www.todomicro.com.ar/electronica-tecnica/767-regulador-de-voltaje-step-up-hasta-83 v-15a-1200w.html (https://www.todomicro.com.ar/electronica-tecnica/767-regulador-de-voltaje-step-up-hasta-83v-15a-1200w.html)
Otra página pro:
https://www.microjpm.com/products/ad49812/

⇒


MARLIN PARA TORPES
1. Instrucciones:
#define: Es una de las instrucciones principales. Le dice a marlin aquellos valores y variables que se encuentran definidos. Se pone generalmente la variable y luego el valor.

#undef: #define pero negado, es decir, quita una variable previamente definida. Difiere con uncomment (//) en que esta instrucción sirve para decirle a marlin que esa variable ya no existe.

#ifdef y #endif: Es una combinación #define y #undef. El microprocesador solo lee las líneas que se encuentra dentro de este #ifdef. Tiene principio y fin. Solo se utiliza si la variable utilizada dentro de esta condición estuvo previamente definida con #define.

IILAH - Alumnos - Grupo 1: Fertonani, Martin, Mele Ientile, Rivera Pascua, Silva Página 25 de 38

#ifndef y #endif: A diferencia del anterior la condición se ejecuta si la variable dentro de ella no se encontraba definida previamente.

2. Velocidad del puerto serie:
La velocidad que viene por defecto en Marlin es 250.000 baudios (comunicación más rápida y sin errores), sin embargo, algunas placas no lo soportan. En este caso lo ponemos en 115.200.
#define BAUDRATE 250000

3. Cosas claves para nuestra aplicación. Todos lo siguiente se encuentra en la carpeta Configuration.h
a) Tipo de placa controladora, en nuestro caso RAMPS 1.4.
b) Debemos poner los datos tanto de autor (nombre de la empresa) como de fecha de compilación, de esta manera podremos saber información de la máquina y si la misma se encuentra actualizada con la última versión de compilación que hayamos creado y cargado. Esto lo haremos mediante las líneas:
#define STRING_VERSION_CONFIG_H __DATE__ " " __TIME__ // build date and time. (una vez subido el Marlin al Arduino, se actualiza la fecha y hora a ese momento)

#define STRING_CONFIG_H_AUTHOR "(none, default config)" // Who made the changes.

En la última línea es necesario cambiar lo que se encuentra entre comillas (None, default config) con algún nombre o el nombre de la empresa.
c) Debemos definir el puerto serie de nuestra computadora que se comunicará con Arduino, por default es el puerto 0. Este valor lo debemos cambiar segun el puerto serie COM de la computadora al cual conectaremos el Arduino o la propia máquina. #define SERIAL_PORT 0
d) Definir si utilizamos las resistencias pullup para los finales de carrera que tienen algunas placas controladoras como arduino. Lo recomendable es activarlas en caso de que tengamos como final de carrera un simple microswitch sin filtro ni nada y desactivarlas cuando tengamos un final de carrera con filtros y demás (los que vienen ya montados en un PCB). La línea de código es:
#define ENDSTOPPULLUPS // Comment this out (using/ at the start of the line) to disable the EndStop pullup resistors.

En caso de que tengamos que activar solo algunas Pullups y no todas, comentamos la línea previamente citada y descomentamos dentro de la siguiente condición negada las que queramos.
#ifndef ENDSTOPPULLUPS

// | fine | EndStop | settings: | Individual | pullups. | will | be
ignored | if | ENDSTOPPULLUPS | is | defined
// | #define | ENDSTOPPULLUP_XMAX
// | #define | ENDSTOPPULLUP_YMAX
IILAH - Alumnos - Grupo 1: Fertonani, Martin, Mele Ientile, Rivera Pascua, Silva | Página 26 de 38

// | #define | ENDSTOPPULLUP_ZMAX
// | #define | ENDSTOPPULLUP_XMIN
// | #define | ENDSTOPPULLUP_YMIN
// | #define | ENDSTOPPULLUP_ZMIN
#endif

e) Chequear si los finales de carrera envían un 1 lógico al ser pulsados, caso contrario, se deberá invertir la lógica para lograr esto. Para poder invertir la los estados normales en Marlin tendremos que poner en “false” o “true”las siguientes líneas.
const | bool X_MIN_ENDSTOP_INVERTING = | true; // | set | to
true | to | invert the | logic of | the | EndStop.
const | bool Y_MIN_ENDSTOP_INVERTING = | true; // | set | to
true | to | invert the | logic of | the | EndStop.
const | bool Z_MIN_ENDSTOP_INVERTING = | true; // | set | to
true | to | invert the | logic of | the | EndStop.
const | bool X_MAX_ENDSTOP_INVERTING = | true; // | set | to
true | to | invert the | logic of | the | EndStop.
const | bool Y_MAX_ENDSTOP_INVERTING = | true; // | set | to
true | to | invert the | logic of | the | EndStop.
const | bool Z_MAX_ENDSTOP_INVERTING = | true; // | set | to
true | to | invert the | logic of | the | EndStop
f) Chequear que el movimiento de los ejes tenga dirección correcta. En caso de que la dirección de movimiento de alguno de los ejes sea incorrecta tendremos que invertir el estado de las siguientes líneas.
#define INVERT_X_DIR | true | // | for | Mendel | set | to

false, for | Orca set | to | true
#define INVERT_Y_DIR | false | // | for | Mendel | set | to

true, for | Orca set | to | false
#define INVERT_Z_DIR | true | // | for | Mendel | set | to

false, for | Orca set | to | true
Ejemplo: El eje X al hacer homing se mueve en dirección contraria y en Marlin estoy viendo que su estado es “True”. Seteo este estado a “False” y listo.
e) Fijar la velocidad de desplazamiento al hacer homing con la línea:
#define HOMING_FEEDRATE | {50*60, | 50*60, | 4*60, 0} //

set | the | homing | speeds | (mm/min)

El orden de los valores son #define HOMING_FEEDRATE (X, Y, Z, Extrusor) y las unidades están en mm/s, pero marlin multiplica este valor por 60 para pasarlo a mm/min. Es decir, supongamos que queremos una velocidad de 3000 mm/min (una locura) ponemos 50*60. El autor recomienda velocidades de 30*60 en los ejes X y Y y 2*60 en el eje Z.

IILAH - Alumnos - Grupo 1: Fertonani, Martin, Mele Ientile, Rivera Pascua, Silva Página 27 de 38 g) En el caso de ser necesario, se puede fijar una velocidad máxima la cual no podrá ser excedida incluso desde el control de la máquina. La línea correspondiente a esta función es:
#define DEFAULT_MAX_FEEDRATE | {500, 500, 5, | 25}

Las unidades se encuentran mm/s y corresponden al eje X, Y y Z respectivamente.
h) Por último, debemos fijarnos las aceleraciones máximas de los ejes por defecto cargadas en Marlin. Para evitar vibraciones y oscilaciones debemos tener las aceleraciones de los motores paso a paso de los ejes con bajas aceleraciones. Para modificar el valor de la aceleración de los ejes se modifican los valores de la siguiente variable definida:
#define DEFAULT_MAX_ACCELERATION {9000,9000,100,10000}

#define DEFAULT_ACCELERATION 3000

La primera línea tiene que ver con las aceleraciones máximas posibles que pueden alcanzar los ejes X, Y y Z respectivamente en mm/s²
sin importar el valor que se incluya en el G-Code. Mientras que la segunda tiene que ver con la aceleración por defecto que tienen los motores paso a paso en caso de que no se especifique dentro del G-Code, también en mm/s²
4. LCD (Full Graphic Smart Controller)
a) Lo primero que debemos establecer es el lenguaje con el cual se mostrarán los mensajes en la pantalla, para esto usamos la siguiente línea de código que se encuentra en el archivo lenguaje.h:
//#define LANGUAGE_INCLUDE
GENERATE_LANGUAGE_INCLUDE(en)
Por defecto se encuentra en inglés (en), lo cambiaremos a español (es).
b) Como nuestra pantalla tiene la posibilidad de insertar una tarjeta SD para ejecutar nuestro G-Code, deberemos activar la SD desde el archivo Configuration.h de Marlin.
//#define | SDSUPPORT | // | Enable | SD | Card
Support | in | Hardware | Console

Si tenemos problemas con la tarjeta a la hora de iniciar nuestro código tenemos como posible solución poner el lector de tarjeta SD en modo lento, para esto descomentamos o definimos la línea:
//#define SDSLOW // Use slower SD transfer mode (not normally needed -- uncomment if you're getting volume init error).
A su vez, Marlin tiene la opción de poder chequear errores de envío y recepción de datos con la tarjeta SD constantemente mediante “CRC check”. Por defecto se encuentra desactivado, pero es recomendable activarlo. La línea a comentar es:

IILAH - Alumnos - Grupo 1: Fertonani, Martin, Mele Ientile, Rivera Pascua, Silva Página 28 de 38

//#define SD_CHECK_AND_RETRY // Use CRC checks and retries on the SD communication.

c) Debido a que nuestra pantalla controladora posee un encoder rotativo (La perilla para seleccionar entre menús, ajuste de parámetro, etc.) debemos configurar la cantidad de pasos que debemos rotar para poder navegar entre los menús con las siguientes dos variables:
//#define ENCODER_PULSES_PER_STEP 1 // Increase if you have a high resolution encoder
//#define ENCODER_STEPS_PER_MENU_ITEM 5 // Set according to ENCODER_PULSES_PER_STEP or your liking
d) Lo siguiente que debemos hacer es descomentar la variable definida que corresponde a nuestra pantalla, esta línea a descomentar es:
//#define REPRAP_DISCOUNT_FULL_GRAPHIC_SMART_CONTROLLER Cabe aclarar que para utilizar este panel tendremos que descargar e incluir la librería U8glib, la misma se puede descargar de GitHub.
e) Por último, desde Marlin podremos ajustar la frecuencia y la duración del Buzzer que posee la pantalla como feedback al presionar el encoder, esto lo haremos modificando el valor de las variables definidas de la siguiente línea: //#define LCD_FEEDBACK_FREQUENCY_HZ 1000 // this is the tone frequency the buzzer plays when on UI feedback. ie Screen Click. //#define LCD_FEEDBACK_FREQUENCY_DURATION_MS 100 // the duration the buzzer plays the UI feedback sound. ie Screen Click.
5. Tenemos la posibilidad de variar la frecuencia de las salidas D8, D9 y D10. Marlin tiene cargado por defecto frecuencias PWM bajas para que no hayan interferencias con el hardware, sin embargo, podremos cambiar el valor de dicha frecuencia modificando el siguiente valor:
#define SOFT_PWM_SCALE 0

Al reemplazar el valor “0” con un “1”, la frecuencia PWM se duplicará. Hay que tener en cuenta que al momento de aumentar este valor, la resolución de la frecuencia (que por defecto es 128) disminuye. Esta función nos servirá para el ajuste del Circuito de Seguridad y la misma se encuentra en la carpeta de Marlin Configuration.h
6. Podemos hacer un homing ultra rápido. Esto quiere decir que en vez de hacer homing en serie de los ejes X y Y (primero uno y después el otro), los ejes se desplazarán diagonalmente de manera tal de hacer homing de ambos ejes al mismo tiempo. Esto lo logramos descomentando la línea:
//#define QUICK_HOME //if this is defined, if both x and y are to be homed, a diagonal move will be performed initially.
Esta función se encuentra en la carpeta Configuration_adv.h

IILAH - Alumnos - Grupo 1: Fertonani, Martin, Mele Ientile, Rivera Pascua, Silva Página 29 de 38

Comandos G

G0 y G1: Marlin no distingue entre uno y otro, para especificar la velocidad de avance del movimiento se utiliza la letra F. Se utilizan para dar la instrucción a los ejes de moverse una longitud específica. Ejemplo:
G1 X12 F2000
Con esto estamos diciendo que el eje X se mueve de manera lineal 12 milímetros a una velocidad de 2000 mm/min. Generalmente se utiliza G0 para diferenciar una operación de mecanizado con una operación en el aire.

G2 y G3: Realiza movimiento de arco, siendo G2 para arco en dirección horaria y G3 en dirección antihoraria. Se especifica el punto final en el eje X, el punto final en el eje Y, con la I se especifica centro de la circunferencia, en el eje X y con la J lo mismo que con la I pero en el eje Y. Sin embargo, este comando no es utilizado para la fabricación de PCB’s. Ejemplo:
G2 X90.6 Y13.8 I5 J10
Con esto estamos diciendo que haremos un arco con dirección horaria, con punto final en X60.6 y en Y13.8, también le estamos diciendo que el centro de este arco se encuentra a 5 mm de la distancia actual en el eje X y a 10 mm de la distancia actual en el eje Y.

G4: Le da la instrucción a la máquina de hacer un retardo por un determinado tiempo, sin embargo no funciona como delay ya que no se para completamente, sino que sigue ejecutando otras instrucciones al mismo tiempo. Se puede expresar tanto en segundos como en milisegundos. Ejemplo:
G4 S1 (le dice a la máquina que espere 1 segundo)
G4 P1000 (le dice a la máquina que espere 1000 milisegundos, lo que es equivalente a 1 segundo)

G21: Con este comando le decimos a Marlin que utilizaremos el sistema de unidades métrico, es decir, que los valores que utilizamos se encuentran todos en milímetros. Ejemplo:
G21
G1 X12 F200

G20: Tiene la función de decirle a Marlin que los valores que se encuentran en el código se encuentran determinados con el sistema de unidades anglosajón, es decir, los valores se encuentran en pulgadas. Ejemplo:
G20
G1 X12 F200

G28: Este comando sirve para hacer homing. Se puede especificar en qué eje hacer homing o no se especifica nada y se interpreta como un homing general para todos los ejes. Ejemplo:
G28 (no especifico nada, entonces todos los ejes hacen homing)
G28 X Y (especifico que el homing solo se lleve a cabo en los ejes X e Y)

G90: Este comando indica a Marlin que todos los valores que se toman de los ejes son absolutos, es decir, que están todos referidos al punto de origen X0 Y0 Z0. Para el enrutamiento de las

IILAH - Alumnos - Grupo 1: Fertonani, Martin, Mele Ientile, Rivera Pascua, Silva Página 30 de 38

PCB’s generalmente se utiliza este método. Ejemplo:
G90
G1 X12 F1200

G91: Con esto le decimos a Marlin que todos los valores de los ejes son incrementales, es decir se mueven dicho valor tomando como referencia la posición actual y no la de origen como lo hacíamos en el G90. Ejemplo:
G91
G1 X12 F1200

G92: Es tal vez el comando más importante de todos para nuestra aplicación, con el le estaremos cambiando las coordenadas reales en las cuales se encuentra la herramienta. En caso de no especificar la nueva coordenada, Marlin interpretará que esa posición de la herramienta es el nuevo origen de la máquina. Ejemplo:
G92 X12 Y30 Z2 (especificamos coordenadas, por lo tanto la posición actual de la herramienta será X12 Y30 Z2).
G92 (no especificamos ninguna coordenada, es decir, ahora la posición actual de la herramienta es el origen).

Comandos M

M3: Le dice a Marlin que prenda el motor
M5: Le dice a Marlin que apague el motor
M114: Muestra la posición actual de la herramienta. Ejemplo: G0 X25 Y14
M114

CNC GCode Controller
A continuación se llevará a cabo una serie de instrucciones de como utilizar el software “CNC GCode Controller”.

Esta aplicación nos servirá como medio para poder comunicarnos con nuestro Router CNC. Básicamente, con el software estaremos enviando comandos y coordenadas a la máquina para que esta lleve a cabo el enrutamiento, el agujereado y el corte de nuestra PCB.

Su interfaz se divide en siete pestañas, de las cuales seis serán de suma importancia. Las pestañas son:

“Simple Controls”: Como el nombre lo indica en inglés, sirve para realizar movimientos básicos de la máquina, como mover la herramienta en los tres ejes, realizar el homing (tanto individual para cada eje como general para los tres), prender y apagar el husillo e iniciar nuestro G-Code inicial.

IILAH - Alumnos - Grupo 1: Fertonani, Martin, Mele Ientile, Rivera Pascua, Silva Página 31 de 38


“Advanced Controls”: En esta pestaña se encuentran los controles avanzados de la máquina, como por ejemplo el avance de la herramienta a una posición específica, prendido y apagado de husillo, la posición actual de la herramienta, hacer homing general, realizar movimientos complejos de arcos y guardar posiciones previas de la herramienta para poder eventualmente volver a cargarlas. Además de este amplio abanico de controles manuales, también tenemos un visualizador del recorrido de la herramienta en la parte izquierda.


“Auto Level”: Con esta pestaña controlaremos y configuraremos todo lo referido con la autonivelación. Más adelante haremos hincapié en cómo realizar este procedimiento.

IILAH - Alumnos - Grupo 1: Fertonani, Martin, Mele Ientile, Rivera Pascua, Silva Página 32 de 38


“CNC Milling”: A través de esta pestaña cargaremos nuestro G-Code, el cual puede ser optimizado. A su vez en la parte izquierda se nos mostrará una cuadrícula con un trazado de nuestro G-Code, podremos cambiar entre diferentes capas que corresponden a cada nivel del eje Z para poder ver el recorrido que hará la herramienta o cualquier otra información importante que se encuentre en niveles de altura diferentes. Este trazado cambiará de color a rojo cuando la herramienta ya lo haya terminado en la vida real. Otro dato importante es que podremos visualizar nuestro G-Code en la parte de derecha inferior, podremos editar línea por línea de nuestro código y además nos avisará si hay algún tipo de error en ellas poniéndose en color rojo o alguna advertencia en color amarillo.

“Communication”: Aquí veremos todos los comandos que son enviados a la máquina. También nos permitirá enviar comandos manualmente.

IILAH - Alumnos - Grupo 1: Fertonani, Martin, Mele Ientile, Rivera Pascua, Silva Página 33 de 38


“Settings”: En este apartado configuraremos todo el software basándonos en las capacidades de nuestra máquina.


Pasos a Realizar para Utilizar el Software

1) Ir a la pestaña “Settings” y cambiar en base a nuestras necesidades la esquina los apartados: Homing: Cambiaremos donde se ubicará el homing total. Este parámetro será seleccionado en base al punto de origen que tomamos al momento de realizar la PCB que se requiera mecanizar
Size of Workingspace: Cambiaremos el valor de esta variable en base al recorrido efectivo total que puede realizar nuestra herramienta en cada eje. Esta opción sirve como seguridad e indica al software el recorrido máximo capaz de realizar nuestra herramienta para que la misma no se choque eventualmente debido a que introducimos una coordenada que sobrepasa

IILAH - Alumnos - Grupo 1: Fertonani, Martin, Mele Ientile, Rivera Pascua, Silva Página 34 de 38 este límite. En otras palabras, es un final de carreras virtual.
CNC/StartGCode: Acá introduciremos el código que se ejecutará antes de comenzar el propio código de nuestra PCB. Generalmente no es necesario, pero existe la posibilidad.
CNC/Spindle ON: Establecemos con que comando prendemos el motor de husillo, el correcto como se mencionó anteriormente es M3.
CNC/Spindle OFF: Establecemos con que comando apagaremos el motor de husillo, el correcto como se mencionó anteriormente es M5.
Autolevel/Options: Con esta opción cambiaremos la altura cero, el máximo recorrido en el eje Z, la altura de retirada, la altura de finalizado y la velocidad de la herramienta durante la ejecución de la autonivelación.
Autolevel/Distance: Definiremos la distancia entre pruebas para la autonivelación. Autolevel/StartGcode: Configuraremos el código inicial antes de comenzar la autonivelación al momento de iniciar este proceso. Por defecto está puesto el comando G28, es decir, el homing general.
Backlash Correction: Esta opción se completa de forma empírica, puesto que es necesario probar el movimiento de los ejes de la máquina. Nos permite corregir el backlash que se genera en la rosca del tornillo roscado.
Device Connected: Con esto elegiremos el firmware que estamos utilizando, en nuestro caso como ya sabemos utilizamos Marlin, por lo tanto, elegiremos esta opción.
Fast Move Feedrate: Configuraremos la velocidad de avance de los movimientos rápidos cargados manualmente mediante la pestaña “Advanced Controls”.

Configuraciones no utilizadas:
CNC/Tool Change: Podemos seleccionar el comando con el cual efectuaremos el cambio de herramienta. En nuestro caso no es necesario ya que utilizaremos una misma herramienta para todas las operaciones de mecanizado.
CNC/G0 Feedrate: Configuración de la velocidad de avance con el comando G0. No utilizaremos esta función ya que Marlin no hace distinción entre G0 y G1, sino que la velocidad de avance para cada movimiento se especificará en la línea del movimiento mediante la letra F.
CNC/Paint Tool Size: Con esta opción definiremos el diametro de nuestra herramienta. No es necesario especificarla ya que es un dato útil solo para el estado de simulación que posee el software.
2) Luego de configurar la aplicación y una vez conectada la máquina con nuestra computadora, estableceremos en la aplicación el puerto de la compu en el cual se encuentra conectada la máquina, establecemos los baudios (ya especificados anteriormente) y presionaremos el botón “connect”. En la siguiente imagen no es posible conectar a ningún puerto ya que no se encuentra conectada la máquina.
3) Ahora que la comunicación de nosotros con la máquina es real, haremos el homing de todos los ejes y moveremos la herramienta manualmente mediante la pestaña de “Simple Controls”

IILAH - Alumnos - Grupo 1: Fertonani, Martin, Mele Ientile, Rivera Pascua, Silva Página 35 de 38 hasta alguna esquina de nuestra placa de cobre virgen previamente instalada en la mesa de la máquina.


4) Una vez que la herramienta se encuentra aproximadamente sobre la esquina correspondiente de la placa, iremos a la pestaña “Advanced Controls” de la aplicación y haremos click sobre el botón “Set Position”, una vez hecho se desplegará una ventana que nos solicita ingresar el valor de esta nueva posición, el objetivo de hacer esto es establecer la esquina de la placa de cobre como el nuevo origen de la máquina, por lo tanto, pondremos estos valores en 0 y continuaremos presionando “Ok”.


5) Llega el momento de realizar la autonivelación, para esto seleccionaremos la pestaña de “Auto Level”, en el apartado de “Position” seleccionaremos las medidas de nuestra placa de cobre o de la parte de la misma utilizada para el mecanizado. Se mostrará una grilla con los puntos en donde la herramienta bajará y tocará la placa. Una vez ingresado estos valores haremos click en “Start” y veremos que la herramienta empezará a moverse haciendo contacto múltiples veces con la placa.

IILAH - Alumnos - Grupo 1: Fertonani, Martin, Mele Ientile, Rivera Pascua, Silva Página 36 de 38


6) Con el proceso de Auto nivelación ya realizado, procederemos a el proceso de mecanizado de nuestra placa virgen. Para esto iremos a la pestaña “CNC Milling” y cargaremos nuestro archivo contenedor del G-Code haciendo click en el botón “Load File” , veremos que se muestra el trazado de nuestra PCB. Luego haremos click en “Optimize”, una vez optimizado se mostrará un cartel que nos muestra el tiempo ahorrado, este tiempo suele ser de unos segundos para aplicaciones simples, oprimimos “Recalc” para actualizar el G-Code y tildamos la casilla de “Autoleveling”. Finalmente clickeamos el botón “Milling” para comenzar el mecanizado.

IILAH - Alumnos - Grupo 1: Fertonani, Martin, Mele Ientile, Rivera Pascua, Silva Página 37 de 38


IILAH - Alumnos - Grupo 1: Fertonani, Martin, Mele Ientile, Rivera Pascua, Silva Página 38 de 38

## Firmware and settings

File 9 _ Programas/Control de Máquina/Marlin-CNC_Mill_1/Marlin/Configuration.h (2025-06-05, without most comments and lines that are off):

#define CONFIGURATION_H
#define CONFIGURATION_H_VERSION 010100
#define STRING_CONFIG_H_AUTHOR "(none, default config)" // Who made the changes.
#define SHOW_BOOTSCREEN
#define STRING_SPLASH_LINE1 SHORT_BUILD_VERSION // will be shown during bootup in line 1
#define STRING_SPLASH_LINE2 WEBSITE_URL         // will be shown during bootup in line 2
#define SERIAL_PORT 0
#define BAUDRATE 115200
  #define MOTHERBOARD BOARD_RAMPS_14_EFF
#define EXTRUDERS 2
#define POWER_SUPPLY 0
#define TEMP_SENSOR_0 998
#define TEMP_SENSOR_1 998
#define TEMP_SENSOR_2 0
#define TEMP_SENSOR_3 0
#define TEMP_SENSOR_4 0
#define TEMP_SENSOR_BED 0
#define DUMMY_THERMISTOR_998_VALUE 25
#define DUMMY_THERMISTOR_999_VALUE 100
#define MAX_REDUNDANT_TEMP_SENSOR_DIFF 10
#define TEMP_RESIDENCY_TIME 10  // (seconds)
#define TEMP_HYSTERESIS 3       // (degC) range of +/- temperatures considered "close" to the target one
#define TEMP_WINDOW     1       // (degC) Window around target to start the residency timer x degC early.
#define TEMP_BED_RESIDENCY_TIME 10  // (seconds)
#define TEMP_BED_HYSTERESIS 3       // (degC) range of +/- temperatures considered "close" to the target one
#define TEMP_BED_WINDOW     1       // (degC) Window around target to start the residency timer x degC early.
#define HEATER_0_MINTEMP 5
#define HEATER_1_MINTEMP 5
#define HEATER_2_MINTEMP 5
#define HEATER_3_MINTEMP 5
#define HEATER_4_MINTEMP 5
#define BED_MINTEMP 5
#define HEATER_0_MAXTEMP 275
#define HEATER_1_MAXTEMP 275
#define HEATER_2_MAXTEMP 275
#define HEATER_3_MAXTEMP 275
#define HEATER_4_MAXTEMP 275
#define BED_MAXTEMP 150
#define PIDTEMP
#define BANG_MAX 255 // limits current to nozzle while in bang-bang mode; 255=full current
#define PID_MAX BANG_MAX // limits current to nozzle while PID is active (see PID_FUNCTIONAL_RANGE below); 255=full current
  #define PID_FUNCTIONAL_RANGE 10 // If the temperature difference between the target temperature and the actual temperature
  #define K1 0.95 //smoothing factor within the PID
  #define  DEFAULT_Kp 22.2
  #define  DEFAULT_Ki 1.08
  #define  DEFAULT_Kd 114
#define MAX_BED_POWER 255 // limits duty cycle to bed; 255=full current
#define PREVENT_COLD_EXTRUSION
#define EXTRUDE_MINTEMP 170
#define PREVENT_LENGTHY_EXTRUDE
#define EXTRUDE_MAXLENGTH 200
#define THERMAL_PROTECTION_HOTENDS // Enable thermal protection for all extruders
#define THERMAL_PROTECTION_BED     // Enable thermal protection for the heated bed
#define USE_XMIN_PLUG
#define USE_YMIN_PLUG
#define USE_ZMIN_PLUG
#define USE_ZMAX_PLUG
#define ENDSTOPPULLUPS // Comment this out (using // at the start of the line) to disable the endstop pullup resistors
#define X_MIN_ENDSTOP_INVERTING true // set to true to invert the logic of the endstop.
#define Y_MIN_ENDSTOP_INVERTING true // set to true to invert the logic of the endstop.
#define Z_MIN_ENDSTOP_INVERTING true // set to true to invert the logic of the endstop.
#define X_MAX_ENDSTOP_INVERTING true // set to true to invert the logic of the endstop.
#define Y_MAX_ENDSTOP_INVERTING true // set to true to invert the logic of the endstop.
#define Z_MAX_ENDSTOP_INVERTING true // set to true to invert the logic of the endstop.
#define Z_MIN_PROBE_ENDSTOP_INVERTING false // set to true to invert the logic of the probe.
#define DEFAULT_AXIS_STEPS_PER_UNIT   { 800, 400, 400, 500 }
#define DEFAULT_MAX_FEEDRATE          { 5000, 5000, 5000, 25 }
#define DEFAULT_MAX_ACCELERATION      { 500, 500, 200, 10000 }
#define DEFAULT_ACCELERATION          300    // X, Y, Z and E acceleration for printing moves
#define DEFAULT_RETRACT_ACCELERATION  800    // E acceleration for retracts
#define DEFAULT_TRAVEL_ACCELERATION   200    // X, Y, Z acceleration for travel (non printing) moves
#define DEFAULT_XJERK                 5.0
#define DEFAULT_YJERK                 5.0
#define DEFAULT_ZJERK                  0.4
#define DEFAULT_EJERK                  5.0
#define Z_MIN_PROBE_USES_Z_MIN_ENDSTOP_PIN
#define X_PROBE_OFFSET_FROM_EXTRUDER 10  // X offset: -left  +right  [of the nozzle]
#define Y_PROBE_OFFSET_FROM_EXTRUDER 10  // Y offset: -front +behind [the nozzle]
#define Z_PROBE_OFFSET_FROM_EXTRUDER 0   // Z offset: -below +above  [the nozzle]
#define XY_PROBE_SPEED 8000
#define Z_PROBE_SPEED_FAST HOMING_FEEDRATE_Z
#define Z_PROBE_SPEED_SLOW (Z_PROBE_SPEED_FAST / 2)
#define Z_CLEARANCE_DEPLOY_PROBE   10 // Z Clearance for Deploy/Stow
#define Z_CLEARANCE_BETWEEN_PROBES  5 // Z Clearance between probe points
#define Z_PROBE_OFFSET_RANGE_MIN -20
#define Z_PROBE_OFFSET_RANGE_MAX 20
#define X_ENABLE_ON 0
#define Y_ENABLE_ON 0
#define Z_ENABLE_ON 0
#define E_ENABLE_ON 0 // For all extruders
#define DISABLE_X false
#define DISABLE_Y false
#define DISABLE_Z false
#define DISABLE_REDUCED_ACCURACY_WARNING
#define DISABLE_E false // For all extruders
#define DISABLE_INACTIVE_EXTRUDER true // Keep only the active extruder enabled.
#define INVERT_X_DIR false
#define INVERT_Y_DIR true
#define INVERT_Z_DIR false
#define INVERT_E0_DIR false
#define INVERT_E1_DIR false
#define INVERT_E2_DIR false
#define INVERT_E3_DIR false
#define INVERT_E4_DIR false
#define X_HOME_DIR -1
#define Y_HOME_DIR -1
#define Z_HOME_DIR 1
#define X_MIN_POS 0
#define Y_MIN_POS 0
#define Z_MIN_POS 0
#define X_MAX_POS 300
#define Y_MAX_POS 300
#define Z_MAX_POS 100
#define MANUAL_X_HOME_POS 0
#define MANUAL_Y_HOME_POS 0
#define MANUAL_Z_HOME_POS 0
#define HOMING_FEEDRATE_XY (10*60)
#define HOMING_FEEDRATE_Z  (5*60)
#define EEPROM_SETTINGS // Enable for M500 and M501 commands
#define DISABLE_M503    // Saves ~2700 bytes of PROGMEM. Disable for release!
#define EEPROM_CHITCHAT   // Give feedback on EEPROM commands. Disable to save PROGMEM.
#define HOST_KEEPALIVE_FEATURE        // Disable this if your host doesn't like keepalive messages
#define DEFAULT_KEEPALIVE_INTERVAL 2  // Number of seconds between "busy" messages. Set with M113.
#define PREHEAT_1_TEMP_HOTEND 180
#define PREHEAT_1_TEMP_BED     70
#define PREHEAT_1_FAN_SPEED     0 // Value from 0 to 255
#define PREHEAT_2_TEMP_HOTEND 240
#define PREHEAT_2_TEMP_BED    110
#define PREHEAT_2_FAN_SPEED     0 // Value from 0 to 255
#define PRINTJOB_TIMER_AUTOSTART
#define PRINTCOUNTER
#define LCD_LANGUAGE en
#define DISPLAY_CHARSET_HD44780 JAPANESE
#define DOGLCD      // Full graphics display
#define SDSUPPORT
#define REVERSE_MENU_DIRECTION
#define INDIVIDUAL_AXIS_HOMING_MENU
#define SPEAKER
#define LCD_FEEDBACK_FREQUENCY_DURATION_MS 100
#define LCD_FEEDBACK_FREQUENCY_HZ 1000
#define REPRAP_DISCOUNT_FULL_GRAPHIC_SMART_CONTROLLER
#define FAST_PWM_FAN
#define SERVO_DELAY 300
#define DEFAULT_NOMINAL_FILAMENT_DIA 1.7500   // (mm) Diameter of the filament generally used (3.0 or 1.75mm), also used in the slicer. Used to validate sensor reading.

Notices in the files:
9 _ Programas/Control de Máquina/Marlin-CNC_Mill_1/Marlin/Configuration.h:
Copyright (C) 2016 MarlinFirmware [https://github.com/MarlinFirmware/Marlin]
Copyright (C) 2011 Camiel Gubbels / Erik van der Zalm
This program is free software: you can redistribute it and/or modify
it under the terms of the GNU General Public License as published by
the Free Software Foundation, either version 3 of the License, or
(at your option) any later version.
